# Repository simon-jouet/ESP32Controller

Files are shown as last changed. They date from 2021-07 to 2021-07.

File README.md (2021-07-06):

# ESP32Controller

ESP32Controller is an open source hardware controller for 3d printers, laser cutter/engraver and other CNC machines.

---

### Overview

There are currently 3 iterations of the board all based on either the ESP32 or ESP32-S2. The ESP32 is a dual core Xtensa LX6 with 34 GPIOs and the ESP32-S2 is a single core Xtensa LX7 with 43 GPIOs and built-in USB support.

  Board | MCU      | Drivers | Mosfets | Thermistors |  Comm. |
  ------|----------|-------- | ------- | ----------- | ------ |
  R3    | ESP32-S2 | 10      | 5       | 5           | USB
  R2    | ESP32    | 5       | 3       | 3           | USB to UART
  R1    | ESP32    | 4       | 3       | 2+2         | USB to UART

### R3 Board

This third iteration of the board moves away from the ESP32 to the ESP32-S2 to gain 9 GPIOs at the cost of having only a single core (albeit more efficient).

Using the newly available GPIOs the number of mosfets and thermistors on the board have increased to 5.

In the R2 board the I2S stream has been used to drive 5 drivers but could address more than that. In the R3 board the number of drivers increased to 10 as the cost of adding support for that many drivers is minimal and should cover most of the use cases.

This board was also designed with TMC2209 drivers in mind (although not required), by allowing UART communication for 8 of the 10 drivers through jumpers on the board and connecting the diag pins to the endstops for the first three driver slots allowing sensorless homing without external jumper wires.

  - 10 pololu stepper drivers over I2S
  - 5 mosfets
  - 5 thermistors
  - 3 endstops (connected to stepper DIAG pins for the first three drivers)
  - USB type C -- OTG port on the ESP32-S2
  - micro SD card slot
  - jumpers for UART communication to the first 8 drivers

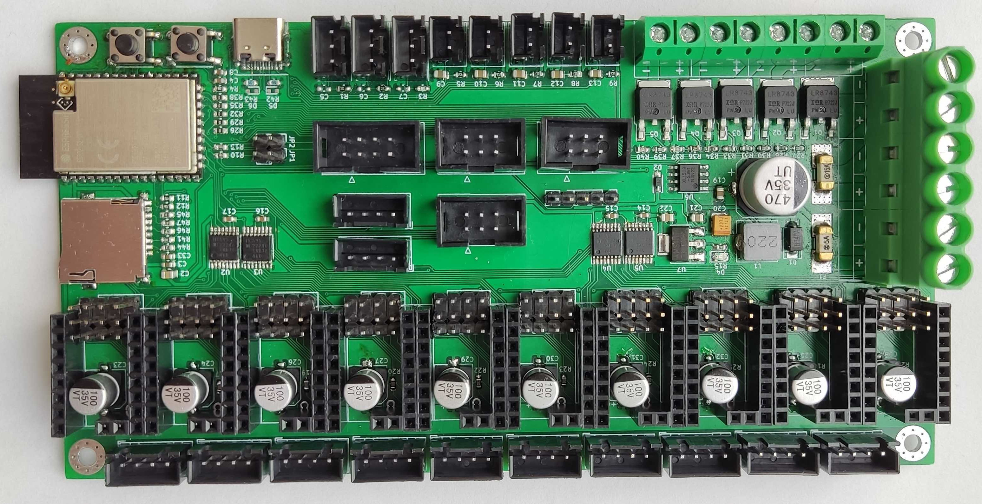
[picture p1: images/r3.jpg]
R3


### R2 Board

The primary issue with using an ESP32 as the main controller for a CNC controller is the general lack of GPIOs on the controller limiting considerably the number of drivers, thermistors and endstpos that can be controlled.

This second iteration main goal was to move away from direct GPIO control of the drivers and instead move to use the I2S stream to provide real time and highly accurate stepper pulses while only using 3 pins on the ESP32.

The redesign also removed some of the unused features of the R1 design most notably the external ADC and the GPIO expander.

  - 5 pololu stepper drivers over I2S
  - 3 mosfets
  - 3 thermistors
  - 3 endstops
  - USB type C -- CH340G USB to UART converter
  - micro SD card slot

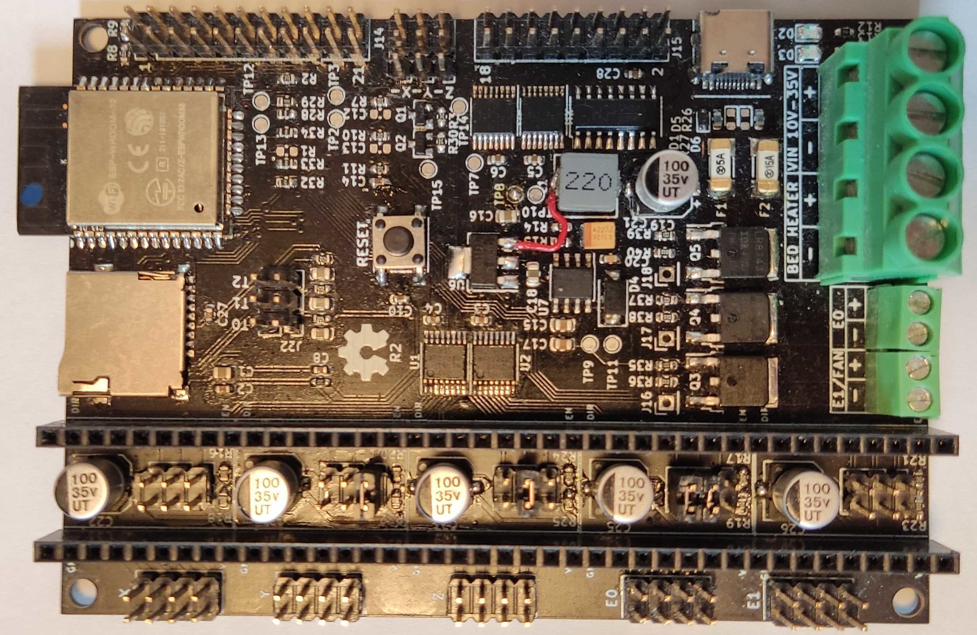
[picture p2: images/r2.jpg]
R2

### R1 Board

This is the first standalone board based on the ESP32. This board was designed as a barebone controller with the minimum required to support an i3 style printer.
 
  - 4 pololu stepper drivers (X, Y, Z, E0) with direct GPIO connection
  - 3 mosfets (Bed, Hotend, Part cooling fan)
  - ADS1015 external ADC for the thermistors (over i2c)
    - 2 thermistors to the ESP32
    - 2 thermistors to the ADS1015
  - SX1509 GPIO expander (over i2c)
    - 3 endstops direct to the the ESP32
    - 3 endstops to the GPIO expander
- USB micro b -- CH340G USB to UART converter
- micro SD card slot

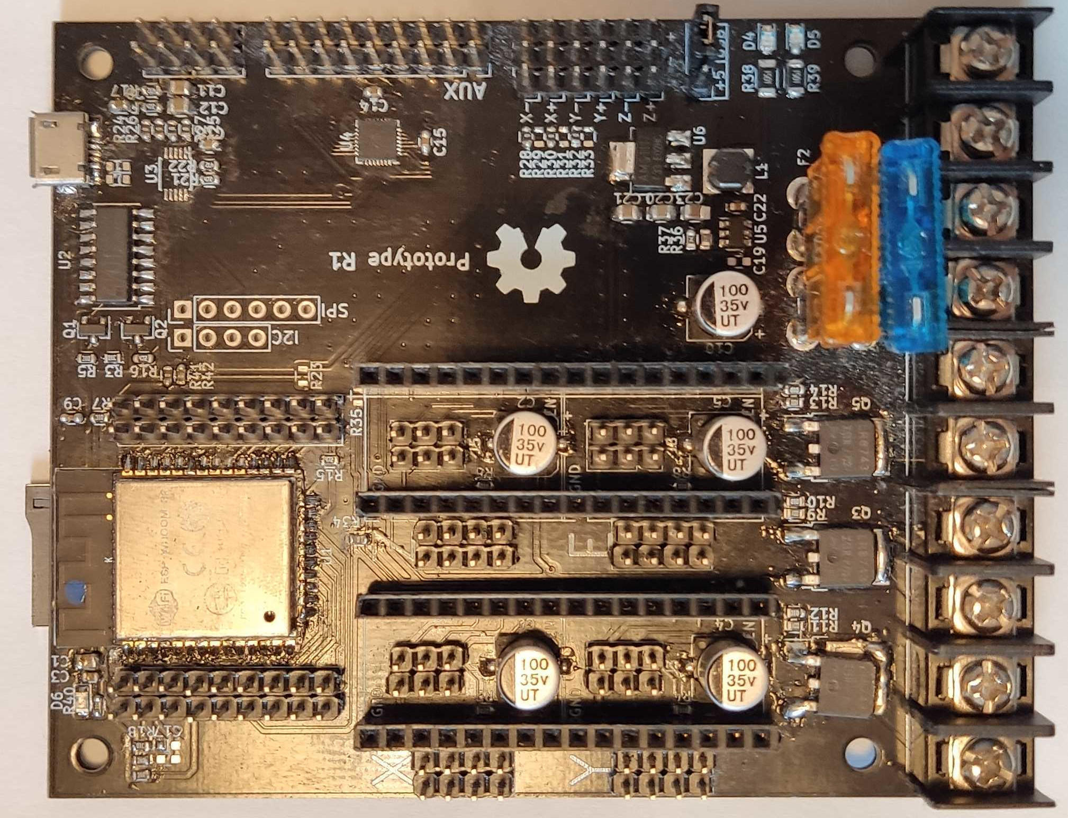
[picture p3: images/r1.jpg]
R1


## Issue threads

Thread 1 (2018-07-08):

Modifications for the R2

simon-jouet, 2018-07-08:
Somes notes for the R2 to consider

* ~~Keep the ADS1015? Either bad batch in the first run or very temperature sensitive when soldering...~~ no need for that anymore
* Add a reset button instead of relying only on DTR
* More compact PCB
* ~~Keep 24V automotive fuses? If so change the socket to something easier to solder. Maybe move to micro autotomotive fuses with sockets~~ switch to 1808 SMD fuses
* Increase the resistance of the witness LEDs as they are super bright at the moment
* Move the SD card slot to the top so the pins can be waved soldered

keyz182, 2018-07-08:
> Add a reset button instead of relying only on DTR

I'd suggest not only a reset button, but two pads or holes for a user to solder a 2 pin header to for wiring up a reset button. Reset is often used as an emergency stop, as it'll stop everything, but bring the software back up to ensure fans are kicked in where appropriate (e.g. hotend, to prevent heatcreep, and subsequent jams).

> Increase the resistance of the witness LEDs as they are super bright at the moment

Definitely! Crazy unnecessarily bright LEDs are getting out of hand :p

As the board sits currently, is it possible to pull a PWM 5v signal from somewhere (e.g. heater)? I ask because it would be interesting to use this board to run a laser cutter, which generally require a 5v PWM for intensity. For e.g. the Duet, this is done by disabling the/a heater, and using it's PWM signal.

simon-jouet, 2018-07-08:
> I'd suggest not only a reset button, but two pads or holes for a user to solder a 2 pin header to for wiring up a reset button. Reset is often used as an emergency stop, as it'll stop everything, but bring the software back up to ensure fans are kicked in where appropriate (e.g. hotend, to prevent heatcreep, and subsequent jams)

So that part is actually already the case, I broke out the pins of the ESP32 so the two top left pins in the header can already be used for that :). At the moment I reboot the board by shorthing both pins with my tweezers...

>As the board sits currently, is it possible to pull a PWM 5v signal from somewhere (e.g. heater)? I ask because it would be interesting to use this board to run a laser cutter, which generally require a 5v PWM for intensity. For e.g. the Duet, this is done by disabling the/a heater, and using it's PWM signal.

At the moment the board runs at 3.3V however there is 5V but it's not exposed (from USB or the SMPS) and regulated down to 3.3V. How much current do you need for the PWM, is it just singalling? because every output pin on the ESP32 can be PWM you can just use any of the available free pin (which isn't much) at 3.3V. You could also use the SX1509 GPIO expander that actually support PWM out - kind of depend how often you need to change the pwm frequency but that would also be at 3.3V. The SX1509 could be powered at 5V to get 5V IO but then would need level translation when talking to the ESP32. I would guess most laser that have a PWM signal input would be quite happy with 3.3V instead of 5V as most devices have high a threshold lower than that (but i'm guesssing - i have a laser module in my aliexpress cart just not ordered yet :))

keyz182, 2018-07-08:
> So that part is actually already the case, I broke out the pins of the ESP32 so the two top left pins in the header can already be used for that :). At the moment I reboot the board by shorthing both pins with my tweezers...

Awesome :)

The PWM is just signalling, so low current. Not sure what would happen at 3.3v, but yeah, it might work, would have to test. No biggie though to add an external level shifter on a separate board for that kind of thing. It's what I've just done on my Duet :)

julianobst, 2018-07-09:
According to the chapter "2.2.1.2 Positioning a ESP32 Module on a Base Board" from the [ESP32 Hardware Design Guidelines](https://www.espressif.com/sites/default/files/documentation/esp32_hardware_design_guidelines_en.pdf), it would be better for the rf performance to remove the copper under/around the antenna or better place the modules antenna outside the baseboard.

simon-jouet, 2018-07-09:
> According to the chapter "2.2.1.2 Positioning a ESP32 Module on a Base Board" from the ESP32 Hardware Design Guidelines, it would be better for the rf performance to remove the copper under/around the antenna or better place the modules antenna outside the baseboard.

Yeah you're right, the current placement is quite far from optimal. I have removed the ground plane on the top layer but not nearly enough to align with the hardware guidelines. Thanks for that I guess with the next rev the ESP is going to move to the right of the board and the antenna is probably going to stick out (which i'm not a big fan off)

julianobst, 2018-07-09:
I think a cutout under the antenna would also do the job. With a cutout you could keep the alignment of the board outline and antenna outline.

simon-jouet, 2018-07-22:
Hey guys, thinking about the R2 of the board - any suggestions on which fuses to go for? I like the automotive fuses like in the current board but they take a *LOT* of space. Did you ever had to replace a fuse - if so how often? (I never had to on my printers/boards).

I very much like https://uk.rs-online.com/web/p/fuse-blocks/7693716/ but they are not cheap. On aliexpress some 1808 SMD fuses are significantly cheaper but they are without a holder an directly soldered on the PCB.

keyz182, 2018-07-22:
They look cool, but also really fiddly to change.

The newer version of the Duet Wifi uses blade type fuses, but they're smaller than the normal automotive fuses (see the 3rd screenshot on their store - https://www.duet3d.com/DuetWifi).

simon-jouet, 2018-12-20:
I found tiny 1808 fuse holders on aliexpress for quite cheap, I ordered a bunch and should get them in January, if they are nice I might use this in the next revision of the board.

https://www.aliexpress.com/item/Hzy-Gold-foot-1808-125V-0451-SMD-Fast-blow-Fuse-0-5A-0-75A-1A-2A/32872911147.html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

simon-jouet, 2019-07-06:
closing #8

Closed 2019-07-06.

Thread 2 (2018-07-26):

[Not an issue] GRBL ported to ESP32

keyz182, 2018-07-26:
Not sure if there's a forum, or somewhere for discussion, so posting here -
https://hackaday.com/2018/07/26/grbl-ported-to-the-esp32/
Worth keeping an eye on.

simon-jouet, 2018-07-26:
hey @keyz182 thanks, yeah I saw this as well over lunch :) I posted a reply to hackaday just in case some people are interested. Regarding the forum no there is nothing for now, if people are interested I could set something up, or maybe start a thread/category on https://discuss.toms3d.org

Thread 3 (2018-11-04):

Request for BOM

vivian-ng, 2018-11-04:
Hi, do you have a BOM? I am trying to figure out what are the specifications of the inductor, mosfets, microSD card shield, diodes, transistors, etc. that you are using in your design.

simon-jouet, 2018-11-05:
Hi @vivian-ng, I've seen some of your messages, sorry for not getting back to you the last few months have been very hectic and I had very little time to dedicate to this. I don't have a proper BOM list yet but I have records of everything i've used.

- Inductor: https://uk.farnell.com/webapp/wcs/stores/servlet/ProductDisplay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
- Mosfets: https://www.aliexpress.com/item/New-IRLR8743-TO252-MOSFET/1695115706.html?spm=a2g0s.9042311.0.0.27424c4dlT22Rw
- microSD: https://www.aliexpress.com/item/10PCS-Push-Push-Type-TF-Micro-SD-Card-Socket-Adapter-Automatic-PCB-Connector-100-brand-new/32881919643.html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
- Diodes: (I think it's in the schematic? IIRC i didn't populate the TVS diodes in the dev version)
- 100uf caps https://www.aliexpress.com/item/E021-50pcs-100UF-35V-6-3mm-7-7mm-SMD-electrolytic-capacitor/32712209859.html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
- screw terminals: https://www.aliexpress.com/item/10pcs-lot-KF7-62-7-62MM-Pitch-2Pin-PCB-Screw-Terminal-Block-Connector-KF7-62-2P/32863208285.html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 (4 and 6 pins versions)
- transistor for the usb to serial https://www.aliexpress.com/item/100PCS-S9014-MMBT9014-9014-Mark-J6-SOT23-SOT-23-NPN-General-Purpose-Transistors-0-1A-50V/32854935087.html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

The rest should be just normal 805 or 603 passives so pretty much anything will do

vivian-ng, 2018-11-06:
@simon-jouet Thank you for giving the links! This will really help me in sourcing for the items.

lkvapil, 2018-11-13:
Hi,

could you share your BOM @vivian-ng ?

Thank you
Lukas

simon-jouet, 2018-11-17:
Guys if you are building one of those boards you can now ignore the ADS1015 and C16. I've figured out a way to get good temp measurements directly from the ADC on board of the ESP32 (especially if you use a revision 1).

I wanted to get rid of the ADS1015 anyway, it's not super cheap and it's a pain to solder (at least the ones I got, half of them didn't work) + we need custom support in marlin.

If you just want to get started with the ESP32 you can also ignore the GPIO expander + supporting circuitry for now. I still haven't added the support in marlin for that (but I will - this gpio expander is very nice, just a bit of a PITA to solder).

Would be great if you could get your own boards - I've been printing with mine for about 50 hours (maybe more considering the number of calibration cubes i've printed). I will try to work on marlin in the coming weeks to add support for some stuff ("eeprom", adc improvements, servo?), once the software is more mature and based on the feedbacks let's design a R2

vivian-ng, 2018-11-19:
@simon-jouet Thanks for the update! I am in the process of putting together a minimalist ESP32 board based on your design, without the GPIO expanders and such as they are not supported in Marlin. Just 4 motors, 1 hotend, 1 print fan, 1 heatbed. Have you tried @luc-github [ESP3D-adapted branch on his Marlin fork](https://github.com/luc-github/Marlin/tree/eps32_webui)? I think it is quite promising for a bare minimal ESP32, since it allows the ESP32 to be controlled via WiFi, given that it doesn't have enough pins to support an LCD controller. Of course, I am going to break out the TX/RX pins so someone with a MKS TFT can easily use it. But ESP32 running on a ESP3D-enabled Marlin firmware just sounds cool. Meanwhile, while designing the minimalist board, I am waiting for the mosfets to arrive (ordered on Aliexpress) so that I can try a jury-rigged setup.

For EEPROM support... that was one of the things that I realized too when I compiled @luc-github fork. This [article](http://tinkerman.cat/eeprom-rotation-for-esp8266-and-esp32/) has a link to an Arduino library for emulating EEPROM on ESP32.

luc-github, 2018-11-19:
I think EEPROM no need to be added there is a space on flash of 4KB for such purpose and as now ESP3D for Marlin use nvs partition instead of EEPROM partition to store settings, this space is fully free

vivian-ng, 2018-11-20:
@luc-github Yes that is basically why I pointed out that article. Arduino Core already has libraries to use ESP32's flash memory as "EEPROM" and this article has an improved version of such a library which I think can be considered for use by any who wants to add "EEPROM" support for ESP32. I was scanning through Marlin and I think the EEPROM-related code is all in one file inside the HAL subdirectory of the respective platforms.

simon-jouet, 2018-11-20:
For the screen you could use an ssd1306 oled screen I think I tried at some point and it works, I might give it another shot though.  Still it doesn't really solve the extra pins necessary if you want a rotary encoder or you might just make it with no pins to spare. My current setup is very similar to yours just a prusa i3 clone with 5steppers (2 for z in parallel) and the usual hotend, part cooling fan and heatbed with an inductive probe.Just a word of caution with your setup, it's what I did at the beginning but make sure you have a clean ground between all the components and try to plug everything (USB host + psu) on the same socket or you might have ground loops.

For the EEPROM emulation, called PersistentStore in marlin, I'm not sure yet if I want to use nvs or spliffs. The marlin api is much more similar to a file seek+write than the blob of nvs and I would rather not use too many write cycles of the flash, anyway I will have a look at that soon.

lkvapil, 2018-12-02:
Hi @simon-jouet,

are you still developing new version or it's in the states, that everything is working ?

Thank you

simon-jouet, 2018-12-02:
Hi @lkvapil,

Yeah I will probably make a second revision of the board at some point, but at the moment it does enough to port Marlin and things might change depending on what can and can't be done in software, so I'm not rushing for a new hardware revision and instead spend some time on the software (even though time has been very limited recently)

At the moment the board and Marlin works well enough to print (it's has been the fulltime board on one of my printers for about 6 months) but there are a lot of features that needs to be implemented and tested. I was hoping to have some people helping with the Marlin HAL but it seems that a lot of people have been focusing on STM32 boards instead (not too sure why, I think the ESP32 is superior in many ways although the number of IOs is a bit of an issue). Anyway, if you want to test the ESP32 for printing either get the current board and it will work or do a makeshift one like @vivian-ng and that should work too.

I'm also open to feedback on the second revision of the board (there is another issue about that). I really like the big 7.68mm connectors I used for power and mosfets because they deal with the high current without issues and you can use crimps which makes everything much nicer. Not sure everybody likes it though. I want to change the fuses to something smaller either micro automotive fuses or go for the 1208 SMD fuses (but then it's hard to swap)... One of the "main" block for a second revision right now is to get the GPIO expander to play ball with Marlin which might change some of the GPIOs allocation and therefore would need another revision of the board. I don't think it's that bad to do, just didn't really had time to work on that

vivian-ng, 2018-12-09:
@simon-jouet Just an update. I put together a Morpheus board and used that to test out the Marlin branch which @luc-github is working on. One thing I realized was the Morpheus board did not have a pull-up resistor for MOTOR_ENABLE, which caused the motors to spin when the ESP32 starts up.

Anyway, I am designing a basic ESP32 printer board (no GPIO extender, etc.) based on the Morpheus design, this ESP32Controller, and RAMPS (plus a few other 32-bit boards with schematics found online). Once the design has been confirmed to be working, I will share it on Github.

vivian-ng, 2018-12-10:
@simon-jouet @luc-github The [schematic for my ESP32-based board](https://github.com/vivian-ng/Hardware/blob/master/MRR_ESP_3DP/Schematic_MRR_ESP_3DP_v0.3.pdf) is now on Github. This is the first version which I feel comfortable with sharing, looking forward to feedback.

v0.1 was a total failure. Don't ask.
v0.2 didn't have the pull-up on MOTOR_ENABLE, and uses the 7.62mm pitch terminals given by @simon-jouet above. But I find them taking up too much space, so I went with 5.08mm pitch terminals like those found on MKS boards (which I own, and have no issues so far with the terminals) for v0.3.

v0.3:
- Basic, just ESP32 with a CH340 so that it can be accessed via USB.
- 5.08mm pitch terminals
- Pull-up on MOTOR_ENABLE
- AUX1 connector, in case anyone wants to connect to a MKS TFT, since there simply aren't enough pins for a Reprap LCD or any other type of controller using a rotary encoder.
- Design consideration is to fit this within 100mm by 100mm (currently, I am working on the PCB layout) so that people can take advantage of cheap PCB production (there is a site which offers 10 PCBs at $2 if the size is within 100mm by 100mm).
- TODO: rename all "+12V" to "VIN" and "+24V" to "VBED" which to me is largely cosmetic, but probably an important detail to real PCB designers.

Any feedback is welcome so that I can make the necessary changes before sending this for a test fabrication.

misan, 2018-12-10:
Having 24V available, why don't you use it too for powering the motor
drivers? You would get more torque at faster speeds, which is good.

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

vivian-ng, 2018-12-10:
@misan
> Having 24V available, why don't you use it too for powering the motor
drivers? You would get more torque at faster speeds, which is good.

Which is why I think a professional PCB designer will likely say my naming conventional is very poorly done. I used "+12V" and "+24V" to differentiate between two inputs, both of which can be 12V to 24V.

The way to read "+12V" is "12V to 24V".
The way to read "+24V" is also "12V to 24V", just connected to another part of the circuit.

I really need to get around to renaming it.

That said, I am also a bit uncertain about how much power the stepper drivers and motors will draw. The terminal for the heat bed is going to be passing a lot of current, and one of the reasons why I didn't connect VMOT to the "+24V" rail is because I don't want too much current through that terminal.

misan, 2018-12-10:
Consider each motor can draw around 1A.

El lun., 10 dic. 2018 9:43, vivian-ng <notifications@github.com> escribió:

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

vivian-ng, 2018-12-12:
I have changed the inputs to VIN and VBED instead of +12V and +24V, plus added a prelim PCB design. Uploaded [here](https://github.com/vivian-ng/Hardware/tree/master/MRR_ESP_3DP). All feedback welcome. Will be sending this for fabrication soon, so that I can give it a test.

Also, I created a [thread](https://github.com/vivian-ng/Hardware/issues/1) on the repo itself for further discussion on my board, so that I don't hijack this repo, which is for Simon's board.

simon-jouet, 2019-07-06:
closing this, the BOM is now in #8 and you have the thread on your repo

Closed 2019-07-06.

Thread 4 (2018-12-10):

[Not an Issue] Hint on I2S Parallel DMA and shift register stepper driving

Aggebitter, 2018-12-10:
I have thinking a lot about this I2S to a shift register. The time resolution should be good and look at this driver for RGB displays:
https://github.com/mrfaptastic/ESP32-RGB64x32MatrixPanel-I2S-DMA
https://github.com/ESP32DE/I2S_parallel_example_drive_a_64x32_display

from thread:
https://esp32.com/viewtopic.php?f=17&t=3188

simon-jouet, 2018-12-10:
Hi @Aggebitter

I've actually been wondering the same and I ordered some sn74hc595 couple of hours before you posted this :), I should get them tomorrow. Hopefully i will get some time over christmas to look into it.

I think if we want to go that way there is no need for the parallel mode of I2S, serial will be fast enough and use less IOs. From the technical reference and if i did my calculations right we should be able to achieve a bit clock of over 1MHz through I2S (40MHz word clock) for 32 outputs which should be plenty.

If we go this way there won't be a need for a GPIO expander as this will free the majority of pins on the ESP32 that we are currently using for step/dir, I just hope it won't be too much hassle getting it to work (especially because i don't have a scope handy)

simon-jouet, 2018-12-11:
@vivian-ng basically the i2s is very similar to SPI, you have some data that is sent serially (and in the case of the ESP32 can also be parallel of configurable width). So for instance you send 32bits of data 1 bit at a time or for instance 4x8 in parallel with 8 outputs. The idea (not mine) is to use the i2s bus with 595 shift registers to allow sending 32bits of data from the ESP32 to the shift registers using only the 3 i2s pins. Using this we should be able to offload the STEP/DIR/EN pins and free up many io pins on the ESP32 while still being fast enough.

So only 3 pins on the ESP32 should be needed for i2s, the data output, the bit clock and the word clock (left/right channel selection in i2s).  So the shift registers are cascaded (so it becomes equivalent to a 32 bit shift register if you use 4, QH' is chained into the next register's SER). The ESP32 i2s output becomes the first shift register SER input and the i2s bitclock and wordclock become the SRCLK and RCLK of all the registers. The output enable pin, is an input on the shift register and it's just used to enable or disable the output of the shift register, we won't need that for this so we should just tie it to ground so the output is always enabled.

Using this technique we should be able to have 32 outputs for only 3 pins used, 15 of them will be used for STEP/DIR/EN for 5 drivers (I guess adding a 5th driver make sense if we have enough outputs) and the 17 remaining can be used for other things (maybe PWM, bang bang ...) or we just populate 2 shift register as it's enough but giving additional 16 pins for ~$0.30 is probably a smarter approach

vivian-ng, 2018-12-13:
I am not very good with how Marlin works, but scanning through the files in Marlin, it seems that `stepper.cpp` under the `modules` subdirectory should be the place to implement the use of shift registers, right? To make it easily configurable, maybe a `#define` statement should be used.

For example, in `pins_ESP32.h`, something like:
```
#ifdef USE_SHIFT_REGISTER
  #define X_STEP S1
  #define X_DIR S2
  #define Y_STEP S3
  #define Y_DIR S4
...
```

Then, in `stepper.cpp`,
```
#ifdef USE_SHIFT_REGISTER
  blah blah blah code for handling movement using shift registers
...
```

 A quick search on Google shows a few Arduino libraries for shift registers. The question is how to implement them for use with stepper drivers. Is Marlin going to send out one pulse to one motor in each "cycle", or will pulses be sent in parallel to all motors being moved in each "cycle"? Meanwhile, I have zero understanding of `stepper.cpp` so I guess I will need to try and find time to understand the code if I am ever going to be able to meaningfully contribute.

misan, 2018-12-13:
My understanding is that a buffer in memory is set and I2S transfers would
be handled by a DMA channel that will be updating the serial register all
the time.

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

simon-jouet, 2018-12-13:
Yeah @misan is right this will have to be handled quite differently from the normal pins as we want to use I2s' DMA for this to be fast enough. Not too sure if we will have to update the serial continuously (which I know is how the ESP8266 examples work) or if we can actually do one-off word send. The i2s support in the ESP32 is much more mature and part of the esp-idf so I hope things are going to be a bit smoother.

Pretty sure the way to do it, is the same way as I did the GPIO expander in the old code (for the first ever board early last year). I want to keep this specific piece of code into the HAL of the ESP32 so we don't pollute Marlin's source code. The way I did it before was to use the MSB of the pin to indicate whether it is a "normal" pin or a pin on the GPIO expander. So pins lower than 128 are normal esp32 pins and pin 128 is pin 0 of the GPIO expander, pin 129 is pin 1 of the GPIO expander...

Doing it this way allows us to implement the entire logic in the HAL (https://github.com/MarlinFirmware/Marlin/blob/bugfix-2.0.x/Marlin/src/HAL/HAL_ESP32/fastio_ESP32.h) and we can abstract from Marlin the fact that these pins are not normal pins.

I received the 74HC595 yesterday, next step is going to be to solder a prototype board to try this out :)

Aggebitter, 2018-12-14:
@simon-jouet @vivian-ng
I know that I had read something about this a few years ago. Well here is those links as well
https://github.com/lhartmann/esp8266_reprap
That is based on one of the ESP8266 godfathers at
https://github.com/cnlohr/esp8266ws2812i2s

simon-jouet, 2018-12-14:
Thanks @Aggebitter I've been through this two in the last couple of days been useful to get some information but code-wise I think it will be quite different. The esp8266 example is very rough, it uses a lot of the low level registers to access the i2s peripheral. The esp-idf for the esp32 contains a proper driver so I think (hope) that the implementation will be much more straightforward and easy to follow than the esp8266 exmaples.

Regarding the board I'm just going to make a very simple board with 4 shift registers, very similar to the one in the esp8266_reprap repo. Hopefully I can get this done this weekend, designing the PCB will be very very straightforward but I want to try to engrave it using my printer so that might take a bit of time :) Once I get something running I will post it here so you can replicate it if you want (the more we are to try this the better)

For the clock of the i2s I won't go in much detail right now but the i2s peripheral works by full 32 bits word at a time even if you only use 16 bits and the maximum rate of it is (if i got it right) 160MHz / 4. So we should be able to achieve a bit clock speed of 40MHz and therefore a word clock of 40MHz/32 = 1.250MHz. What I used as a reference is a bit of a back of the envelope math, but the A4988 requires a minimum of ~4us pulse time (the TMC are faster than this but it was more to check things out). 4us is 250kHz so we've got plenty to spare even if we try to step as fast as we can. Reallistically the 74hc595 won't be able to be clocked at 40MHz but I think it should work out okay even if we go lower than that

Aggebitter, 2018-12-14:
@simon-jouet When you are ready with your prototype schematics can you post it asap ?
The shift register can't be connected in so many ways :) but what pins would you use in the ESP32 and what pins för the stepper drivers? Are we going for four 74HC595 from the start ?

I've got the time this weekend as well to build a prototype and got the tools for probing and sample the output if you run into problems.  I'm more into electromechanics than programming (just novice basic skills and knowledge in C++/C)

simon-jouet, 2018-12-16:
@Aggebitter Here is the basic schematic [i2sexpansion.pdf](https://github.com/simon-jouet/ESP32Controller/files/2683606/i2sexpansion.pdf).

I've tried to mill the PCB using my printer and it wasn't a great success (and my neighbours probably didn't like me very much) so I just it setup on breadboard for the time being. I've managed to hook up my Saleae clone logic analyzer too and it looks like it's doing the job well enough so that's a good start. (I might etch a board but my 2d printer died :D)

For the pins to use on the ESP32 I'm not sure yet and it doesn't matter too much but i'm considering using GPIO17/GPIO16 and GPIO0 so we still have all the rest available (HSPI/VSPI/I2c...)

For the 5V operation I think we might be able to get away with it without level shifting, if we want to run at 5V. We already have on the board 5V from either the USB or the buck converter than can be used to supply the shift registers and the 3.3V output of the ESP32 should be high enough for the input of the shift registers. The issue would have been if the shift registers output something to the ESP32 but that's not the case.

Now i will have to look a bit more into i2s, from the little time i spent on this yesterday it looks like the bclk and channel selection continue to run even if the transmit buffer is empty. I guess on the esp8266 example that's why they continuously send the same data, so I need to look into that either to keep queuing data, make the buffer cyclic so it resend the same data over and over again or be able to switch off the clocks when the buffer is empty.

misan, 2018-12-16:
@simon-jouet 74HC595 can work from 2 to 6V http://www.ti.com/lit/ds/symlink/sn74hc595.pdf
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
Aggebitter, 2018-12-25:
@simon-jouet  Can writing to the registers be handled by the stepper interrupt routine in Marlin ?
Why I'm asking is that with this solution the implementation to HAL should be straight forward but we do not free up cpu cycles. I'm I right ?

I was thinking complete the other way around. By giving FreeRTOS a Core0 task with decent priority just to feed the DMA ring buffer (The bigger size of buffer the lower priority). The stepper interrupt would just write to that buffer instead of pulling GPIO's. As we can toggle the stepper pins at more than 400kHz the limit is in what time resolution we would need. And the time resolution in not an issue.

As an example.  If we use a GT5 pulley with 20 tooths and 256 microsteps. The step rate will be 256 000  steps/sec and give 100mm/sec on a 200 step/rev stepper motor. If we put in the numbers that I've got (probably not maxed out yet) on the skift register that is 416 000 steps/sec and with the same hardware setup it gives us 162.5 mm/sec in movement

So what if we "miss" aka linear jitter, a step in the time domain. One micro step is 0,000390625 mm that's maximum error at all speeds for all axis! At slower rates this linear jitter will reduce more but still be there. Conclusion: We are way below the mechanical error in the stepper motor itself.

The size of the ring buffer is only a matter when the stepper movement has to interact with other interrupts as when homing and probing. But let us look at the linear jitter again. With a ring buffer at 1024 we will get a limit interrupt somewhere in the +0.4 mm range. That sounds like a bad numbers. Well that was at 162.5mm/sec probing ;-). At feed rate 60mm/min we will move 1mm/s. The ring buffer will be have a round trip of less than 0.0025 sec (ring buffer size / word clock), that is again much lower than the stepper motor error.

My thinking with the ring buffer is that we would not need any semaphores or other task write handlers for that buffer in FreeRTOS. Just do a write as it is a buffer. Add a new data flag to the function and the ring buffer could loop the same data as long as no new data has arrived. No interrupts just a loop that feeds the DMA with the same data as long as it has not change. And if
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

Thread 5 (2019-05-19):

[Question] Where to define I2S_STEPPER_STREAM and any ideas about temperature readings?

felixstorm, 2019-05-19:
Hi Simon,

thanks for your great work! I upgraded my Creality Ender 3 to use an ESP32 with TMC2208 stepper drivers connected to I2S based on your coding and on your schematic here in the r2 branch and it works like a charm - just finished my first print today!

Two questions came up that you might have an answer to:
* Where did you define `I2S_STEPPER_STREAM`? I thought it would be best suited in `pins_ESP32.h` but then it seems to be missing inside `stepper.cpp` (all moves ended up terribly slow as `STEPPER_TIMER_RATE` had been defined as if used without I2S). I ended up putting it in `platformio.ini` as a build flag, but maybe you have a better idea?
* Temperature readings vary massively. This might have to do with the ESP32s ADC - is that just the way it is or have you been able to figure out a better solution?

Thanks again for your great work and kind regards,
Felix

simon-jouet, 2019-05-20:
Hi @felixstorm,

Great to hear that you are using the HAL especially with the I2S not many people do unfortunately (although I guess when a board becomes available more people will)

> Where did you define I2S_STEPPER_STREAM? I thought it would be best suited in pins_ESP32.h but then it seems to be missing inside stepper.cpp (all moves ended up terribly slow as STEPPER_TIMER_RATE had been defined as if used without I2S). I ended up putting it in platformio.ini as a build flag, but maybe you have a better idea?

I will have to double check with my local version when I have access to it but IIRC it was defined in the HAL.h of the ESP32's hal.

>Temperature readings vary massively. This might have to do with the ESP32s ADC - is that just the way it is or have you been able to figure out a better solution?

So the ESP32 ADC is far from perfect but it should be more stable than what you describe (I also think that Marlin can be tweaked to work better especially when the ADC can be sampled quickly). The first thing to check is which version of the ESP32 you are using, the ESP R1 is much better because it contains a factory built-in calibration curve for the ADC as well the proper VREF. If you use a R0 then you can calibrate the VREF by hand (although I would just recommend switching to an R1). You can also check the voltage reference of your voltage divider make sure it's very close to 3.3V. Check that the resistors you have used have a good tolerance. And finally make sure to retune your PID.

Hope that helps, I haven't really touched this in a while, but I'm still planning to get back to it at some point :)

Simon

felixstorm, 2019-05-20:
@simon-jouet - thanks for your reply. The I2S path really seems a very clever (and cheap) way to go to get more GPOs and perfect stepper timing. I really do not know either why people do not use it more often.
For me it was quite simple: I wanted to upgrade my Ender-3 to TMC2208 and WiFi, but also wanted to keep LCD, SD card etc., so I needed the pins and so I thought to give it a try.

About `I2S_STEPPER_STREAM`: I already did some tweaks to my local copy to be able to define `I2S_STEPPER_STREAM` in `pins*.h` (where it makes sense the most IMHO since the pin numbers defined there target I2S 128+), I just need to verify that it does actually work, rebase against a current version of `bugfix-2.0.x` and then I would file a pull request to https://github.com/MarlinFirmware/Marlin.

I will post it here after I did the polishing so you can have a look and potentially object.

felixstorm, 2019-05-20:
About the temperature readings: I did do a PID retune, but I do have to check the ESP revision. It's not that the readings are off a certain amount or percentage, but they go up and down permanently between 5 and 8 °C. Do you remember if you had stable temperature readings on your printer?

felixstorm, 2019-05-20:
Ok, this would be the patch for `I2S_STEPPER_STREAM`:
```
 Marlin/src/HAL/HAL_ESP32/HAL_timers_ESP32.h | 6 ++++++
 Marlin/src/pins/pins_ESP32.h                | 2 ++
 2 files changed, 8 insertions(+)

diff --git a/Marlin/src/HAL/HAL_ESP32/HAL_timers_ESP32.h b/Marlin/src/HAL/HAL_ESP32/HAL_timers_ESP32.h
index 7fbaa5222..3d2d777de 100644
--- a/Marlin/src/HAL/HAL_ESP32/HAL_timers_ESP32.h
+++ b/Marlin/src/HAL/HAL_ESP32/HAL_timers_ESP32.h
@@ -28,6 +28,12 @@
 #include <stdint.h>
 #include "driver/timer.h"

+// need this to pull I2S_STEPPER_STREAM definition from pins_*.h based on configured board
+#include "../../inc/MarlinConfig.h"
+// need to also include pins.h explicitly here as the above statement will be ignored if HAL_timers_ESP32.h
+// is being included from inside MarlinConfig.h / HAL.h (but before pins.h)
+#include "../../pins/pins.h"
+
 // --------------------------------------------------------------------------
 // Defines
 // --------------------------------------------------------------------------
diff --git a/Marlin/src/pins/pins_ESP32.h b/Marlin/src/pins/pins_ESP32.h
index 9901dde20..dad1e0d81 100644
--- a/Marlin/src/pins/pins_ESP32.h
+++ b/Marlin/src/pins/pins_ESP32.h
@@ -40,6 +40,8 @@
 //
 // Steppers
 //
+#define I2S_STEPPER_STREAM
+
 #define X_STEP_PIN         128
 #define X_DIR_PIN          129
 #define X_ENABLE_PIN       130
```

vivian-ng, 2019-05-20:
@felixstorm One suggestion is to create a separate pins_xxxxx.h file for your current setup. This way, the pins_ESP32.h can be the standard pins file for all boards based on the ESP32 (like pins_RAMPS.h) and every adaptation of it is a separate pins file.

Also, I am curious as to how you can connect the Ender-3's LCD to this setup. I am trying to figure out how the LCD's pins work...
So far, what I can glean out for the [Creality v1.1.2 board](https://github.com/Creality3DPrinting/CR10-Melzi-1.1.2/blob/master/Circuit%20diagram/Motherboard/CR-10%20Schematic.pdf)'s LCD connector:
Pin 1: VCC 5V
Pin 2: LCD_PINS_ENABLE (connected to ATMEGA1284's SDA pin)
Pin 3: LCD_PINS_D4
Pin 4: RESET (is this the EN pin of the ESP32?)
Pin 5: BTN_ENC (connected to ATMEGA1284's SCL pin)
Pin 6: BEEPER_PIN
Pin 7: BTN_EN1
Pin 8: BTN_EN2
Pin 9: LCD_PINS_RS
Pin 10: GND
I guess for the ESP32, most of the pins to use this LCD display can be the freed-up pins (IO25, IO26, etc.) but just wondering if LCD_PINS_ENABLE must be SDA and BTN_ENC must be SCL?

felixstorm, 2019-05-20:
@vivian-ng Yes, I also did create my own board and `pins_ESP32_FS_ENDER3.h` file (https://github.com/felixstorm/Marlin/blob/Felix_Ender3_ESP32_2.0.x/Marlin/src/pins/pins_ESP32_FS_ENDER3.h), but since `pins_ESP32.h` also references stepper pins above 128 which need I2S, I thought it would be helpful to have it in `pins_ESP32.h` as well.

And for the LCD on the Ender-3 take a look at the attached PDF. This is my current setup (R160 & R161 are not populated, based on @simon-jouet's work in his r2 branch) which works nicely on my Ender-3: [201904_Esp32ReprapController.pdf](https://github.com/simon-jouet/ESP32Controller/files/3198646/201904_Esp32ReprapController.pdf)

Marlin needs a few more fixes for ESP32 to work with the current bugfix-2.0.x branch, but I will hopefully be able to file the corresponding pull requests within the next few days:
https://github.com/felixstorm/Marlin/commit/6d3199539e919592f7f4926ab2c75e227cca6d1c
https://github.com/felixstorm/Marlin/commit/01011ac973846a3e5b46db92b98409621a3e261d
https://github.com/felixstorm/Marlin/commit/6281e378af18b5389db730edb92bfff250ea2e1e
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
edsonbrusque, 2019-05-29:
Hello @felixstorm.

I'm interested about your ADC noise.

It would be useful to know if the variation is in your readings or in your actual bed temperature. Are you seeing this variation only on the display? Do you have any means to measure the actual nozzle and bed temperatures (a thermometer with a logger) or the voltage at the ADC pins (an oscilloscope)?

If the temperature variation on the LCD is very quick (like changing +/- 5% all over the place) it's probably noise on the ADC pin.

If it's a more sinusoidal variation with a more or less defined duration (like going from 195% to 205% in 10 seconds and back) it would suggest poor PID tuning.

A quick way to filter noise is using larger capacitors (C30, C31 and C32 in your schematic). 10k and 100nF (as in your schematic) give a time constant of 1 us, which is usually adequate regarding high-frequency noise.

You also can't make this time constant very large (like changing to 100 uF capacitors that will give you one entire second time constant) as the PID would probably overreact and have slow and large oscillations).

I have an Ender-3 and just learn about this ESP32Controller project. I would like to build it. Maybe it's time to order some stepper drivers... :)

felixstorm, 2019-05-30:
@edsonbrusque I still have not figured out what exactly causes the noise in the temperature readings, but due to your question I started to dig again today. Unfortunately I still do not have an answer, but I have a few findings:
* It is not due to PID tuning as there also is noise when I switch off the heater and the nozzle slowly cools down.
* Removing the step down converter and powering the ESP32 just via USB did not make a difference.
* Switching the ESP32 module to a different one that I had lying around did not make a difference.
* But: Connecting an ESP32 on a breadboard just with jumper wires on `GND`, `3V3`, `NOZZLE` and `NOZZLE_T` to my board does make temperature readings work fine. When the heater is powered, I can see nice sinusoidal variations from (probably sub-optimal) PID tuning and also when I switch off the heater there are nice decreasing readings without any errors .

Hopefully I will have some more time tomorrow and then I'll try to check wire by wire what causes the noise.

BTW: The capacitors used for the thermistors are C20 and C21 which are already 4.7 uF (and adding even larger ones did not make a difference either).

edsonbrusque, 2019-05-30:
Hello @felixstorm. It seems to me that the stepper drivers are injecting noise on your VCC (+3V3).

Is it possible to power the drivers from the +5V line?

Or can you have a separate regulator from 5V to 3V3 to power just the drivers?

The development boards don't have beefy capacitors and power regulators. I would rely on it just to power the components on the development board itself. You may even need larger capacitors (like 2 x 470uF x 16V) on the development board 3V3 just to lower the spikes caused by WiFi communication.

Maybe some bigger capacitors on the 3V3 and 5V power lines (on strategic places around the board) would help. I see that you have capacitor for the +24V line close to the drivers, but there's no capacitors for the VCC line. I would not assume that the (cheap?) stepper driver modules have adequate decoupling.

Which stepper drivers are you using?

Can you provide the board design file?

felixstorm, 2019-06-02:
It turned out for the noise on the temperature readings to be caused by the I2S lines in combination with my quick-and-dirty board layout. I had expected the whole I2S path up to the drivers to fail, but not for it to have unwanted side effects on other areas. But 2 MHz is more than I usually deal with ;-)

As I anyway had the plan to update my board layout a bit, I will do that and let post my findings up here.

@edsonbrusque I had already completely removed the stepper drivers for the tests and even the shift register ics. I also did try attaching different kinds of capacitors to the different power lines. WiFi is off currently (primarily to reduce upload and Marlin boot time). The drivers I use are FYSETC TMC2208.

Felix

felixstorm, 2019-06-08:
Finally I seem to have been successful. The third revision of my board works nicely and I do not seems to have any unusual noise in the temperature readings anymore.
Details including board layout can be found [here](https://github.com/felixstorm/Creality_Ender_3_ESP32_Board).

Thanks again for everybody's help!

Closed 2021-07-06.

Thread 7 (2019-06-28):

R2 routed?

KanyonKris, 2019-06-28:
@simon-jouet, very nice project!
The schematic looks nice. I opened the PCB layout and I see the part footprints but no traces, just the net lines. Is this correct or do I have something wrong?

simon-jouet, 2019-06-28:
Hi @KanyonKris

Thanks, I haven't routed the R2 board because I'm still tweaking it a bit, if you want to see a routed version @Ringel pushed a MR for one. I haven't tried it but if you wait a bit @Ringel should be able to tell you if it works or not.

I've done few more Tweaks to the schematic since then and will continue a bit over the weekend. I also think I've found a decent layout so the next step will be to clean that up a bit and start the routing. With the layout I've drafted for now we should have the full board in the same footprint as an arduino mega

KanyonKris, 2019-06-28:
Thanks for the reply. I'll check out Ringel's board and watch for your updates.

simon-jouet, 2019-07-06:
closing #8

Closed 2019-07-06.

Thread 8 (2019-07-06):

R2 preview and BOM

simon-jouet, 2019-07-06:
Okay so I've finished the R2 and ordered some PCBs, here is the 3d render

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

I started the BOM and my current estimated cost for the components + PCB is about ~£10 ($12.5) of course on top of that there is the assembly cost and wastage but that's very dependent on the number of boards being made (and for the time being i do it myself)

[BOM.xlsx](https://github.com/simon-jouet/ESP32Controller/files/3364564/BOM.xlsx)

While doing the BOM i've noticed I've made two mistakes in footprints for the diodes, I was hoping to get a 603 package for the diodes but that's not the case, shouldn't be too much a problem for this batch but I will have to get it fixed.

shawe, 2019-07-20:
Thanks for sharing your work.
Do you try it (or can do it) with this GRBL fork? https://github.com/bdring/Grbl_Esp32 Looks interesting have a same board that can work well with both projects.

Aggebitter, 2019-07-21:
Is there a possibility to by one assembled or un assembled from you?

Aggebitter, 2019-07-21:
@shawe The GRBL_ESP32 does not use shiftregisters for the stepper motors. But you can configure Marlin to work as an router/Mill

shawe, 2019-07-21:
Thanks for your answer @Aggebitter, then Marlin is more interesting to me at least for start. I asume that each project are more specific to each work, but don't look for if someone can do both.

I'm interested also in get one, I try a quote from jlcpcb and seems to be available 5 boards at 2$ (offer only for the first buy and also applicable for more units) but I'm not familiar to solder SMD components and also don't have the needed tools to work with that precision.

Aggebitter, 2019-07-26:
@shawe I'm running GRBL_ESP32 on my small router, even tryed to get GRBL_ESP32 interested in using shiftregisters but no response on there part.

vivian-ng, 2019-07-31:
@simon-jouet Can you share the settings you had to make in Configuration.h and pins_ESP32.h to [test out the OLED](https://github.com/MarlinFirmware/Marlin/issues/14345#issuecomment-515755280) and possibly ILI9341? I am wondering about the display/LCD option to set in Configuration.h, and the settings for SDA pin, SCL pin, I2C address for the OLED display, and the different pins for the ILI9341.

simon-jouet, 2019-07-31:
> Is there a possibility to by one assembled or un assembled from you?

For the time being I don't have enough components to assemble more than a handful of boards so probably not (I will send one to thinkyhead and probably to Luc for dev). I've ordered a few more components so i might be able to assemble a few more boards. Let's see when I get the components but I would rather not assemble too many myself as it takes a while (maybe ~2 hours per board) and sending the individual components not soldered will be a mess with the amount of SMD resistors/cap/ics. If enough people are interested we could potentially get a batch assembled in China but I'm not too sure what would be the price of that.

> @simon-jouet Can you share the settings you had to make in Configuration.h and pins_ESP32.h to test out the OLED and possibly ILI9341? I am wondering about the display/LCD option to set in Configuration.h, and the settings for SDA pin, SCL pin, I2C address for the OLED display, and the different pins for the ILI9341.

For the OLED it's relatively straightforward, just connect the screen D0 and D1 to SCL and SDA in the esp32 (pin 21, 22), connect the enable to the enable pin of the ESP32 and tie D/C to ground (https://electronics.stackexchange.com/questions/164680/ssd1306-display-spi-connection-or-i2c-according-to-resistors). Once that's connected in your configuration.h comment out `//#define U8GLIB_SSD1306` and modify your platformio.ini for the esp32 like that

```diff
 lib_deps =
+  ${common.lib_deps}
   https://github.com/me-no-dev/AsyncTCP.git
   https://github.com/me-no-dev/ESPAsyncWebServer.git
 lib_ignore  =
-  LiquidCrystal_I2C
   LiquidCrystal
-  NewliquidCrystal
-  LiquidTWI2
   TMC26XStepper
   c1921b4
-  SailfishLCD
-  SailfishRGB_LED
```

For the ILI9341 I haven't really tried yet, I had a quick look but the current code is quite specific for STM32 IIRC so there will be some dev required for that (and it's not very high in my priorities to get that working for now)

shawe, 2019-07-31:
> > If enough people are interested we could potentially get a batch assembled in China but I'm not too sure what would be the price of that.

@simon-jouet I'm asking for a quotation on PCBWay of 20 units (to get an idea), comparison price later. Maybe 20 are a lot of they at this time, I don't know, but is the most affordable option for few units.

Also, maybe there are better alternatives to make it, but this company can do it all process without wasting your time. I upload your gerber files, and your BOM list and maybe tomorrow they fill it the quotation.

Quotation at this moment:
- 2 Layers Size 102x71mm 1.6mm Product No.:W234586ASH1 [PCB Production]
  -  20 units at $37.00 - $1.85/unit
  -  5 units at $24.00 - $4.80/unit
- SMT for PCB No. W234586ASH1 [PCB Assembly ]
  -  20 units at $30.00 - $1.5/unit
  -  5 units at $30.00 - $6/unit
- Components
  - Waiting for reply of PCBWay (I edit this when receive a notification)
- Shipment
  - Unknown at this moment
- Your fees for your work

They also promoted open source: Share&Sell _This feature is for open source enthusiasts who would like to share the cool projects to others and earn commission._

Maybe this last option is more comfortable to you, and also allow us to get one fully assembled.

If anyone is interested in how this company work, I found this promoted video that is a tour on this factory https://www.youtube.com/watch?v=24ehoo6RX8w

simon-jouet, 2019-08-02:
Hi @shawe,

Thanks for looking into that, I had a brief look couple of days ago at elecrow that provides similar services but didn't go as far as asking for a quote. 20 might be reasonable, I might post on Twitter in the next few days to check who would be interested and point them to here, even if there are couple extras it's not too big a deal.

I will revise the the BOM looks like there are quite a few things that are to be fixed. But looking at the prices it seems more expensive that what I would have expected, let's see once I revised the BOM and let's see what this includes. Do you know what the total of $452 includes?

Before we go for a batch I need to slightly revise the current PCB there are two footprints that are incorrect in the current board (two diodes) and I want to add a couple of headers for the +5V and +3.3V (realised this when I tried to connect a BLTouch...)

I think the open source approach is good, it will save in admin time plus if I need to ship the board from the UK it's going to be quite expensive.

shawe, 2019-08-02:
I'm not sure with the prices, because they change it without reason and without any explanation, and not respecting what I see first day, but looking their page seems to be this:

- $37 for all PCB Production
- $410 for all PCB Assembly (this part appear first time to $30 for <5, but seems to be per unit)
- $452 for all PCB components, the double than is in your list (this part is not yet filled on the quotation, I suppose you see it on the replyed BOM)

Using this prices as reference, the board fully assembled seems to be $44.95/unit

This appears on my quotation (it's in spanish):
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

@simon-jouet if you prefer it, you can upload this files and be directly in contact with PCBWay to clarify all that you want, you only need some minuts to upload your files, and wait for the reply as I attached here.

simon-jouet, 2019-08-02:
Looks very very expensive to me, I might be missing something but here the assemble board is about 3 times the BOM which I think is a bit unreasonable. (the BOM is wrong and a bit too high but still wouldn't change much). My BOM is ~£10 ($12) including the PCB with components that have been shipped individually from China. Here the cost components is higher while they weren't shipped, and the BOM price doesn't include the PCB. Finally we probably need to add shipping + import duties on top of that.

The prices in my BOM are in GBP (£) and they use ($) so their is some difference from that, but even with that there is quite a big difference.

I might check with Elecrow to see how much that would be and I might ask around to see if people have some info about this and if anyone has some experience with that please let me know :)

shawe, 2019-08-02:
I think the same, it's a big difference, maybe they are using another components in comparison with your list. Maybe later I can check component to component to found the problem comparing both BOM list.

The good part, is that they include part numbers, and can be checked or change it to some specific parts, reducing this difference but require an additional check that maybe is also need with Elecrow.

shawe, 2019-08-02:
I use the BOM replied by PCBWay, and fill it with Mouser and Digikey prices (always per unit, I know is the most expensive way) and probably I do a mistake some parts. Also there are some parts that I don't know how to found it.

Anyway, the final price is a little less than buying all individually, but of course not at same price than buying at the next level for quantity and also DIY.

[W234586ASH1-20sets-BOM 2019-8-1.xlsx](https://github.com/simon-jouet/ESP32Controller/files/3462677/W234586ASH1-20sets-BOM.2019-8-1.xlsx)

The PCB Assembly on Elecrow must be very similar, because they also have an online estimate quotation, and the price is calculated based on unique parts, holes, SMT pads, ... I don't fill this form on PCBWay, I only attach the BOM that is incomplete to a quotation and wait for a more realistic quotation.

If I'm not wrong, this form is not well completed on the other site, because I get the same start price with Elecrow. It's filled like in this image:

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

shawe, 2019-08-16:
Sorry for saying this again, but people from PCBWay are asking me again if the BOM list was reviewed with things they attached on file to be able to finish the quotation.

Closed 2021-07-06.

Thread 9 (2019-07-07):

Malyan, and monoprice have been paying attentoin and made a control board using the ESP32 SoC

Sniffle, 2019-07-07:
This is the control board in use on the Monoprice MP10 and MP10 Mini, which is rebranded from Malyan with part numbers MA10 and MA10 mini.

https://imgur.com/a/0MB0AIy

If the imgur album link fails, I will make the images public and link to them directly.

The SoC in use seems to be the ESP8266EX, which has a touch display attached to its back, a daughter board for USB and SDCard.  A 16pin ribbon cable runs to the heater and stepper board.  power is input from the power supply to the stepper control board and send along the 16 pin cable to the ESP32 main control.

That's as far as ive had a chance to dig into this.

If this piques your curiosity I'd be happy to put time towards helping get this done.  If there is any information, pictures, diagnostics, etc.  Id be happy to help.

display and ESP control board - https://www.monoprice.com/product?p_id=39107
Stepper heater board - https://www.monoprice.com/product?p_id=39106

simon-jouet, 2019-07-10:
Thanks @Sniffle for the info, it would be good to have a better look at it.

My first impression is that the esp32 is not used for printing but is used a the "screen" for the printer. My guess is that the ESP32 drives the screen and provides a webUI but the printing is done by another microcontroller (likely an atmega) and the ESP32's serial is connected to the Atmega's serial.

I might be totally wrong and would be nice to see a manufacturer using the ESP32 directly. But if you look at https://images.monoprice.com/productlargeimages/391062.jpg you can see below the capacitor a QFP package with what looks like 64 pins.

Ringel, 2019-07-10:
Its a ESP8266 - not a ESP32!
Yes looks like it drives the display ... maybe via the 2 8bit shiftregisters 74HC164 and the XPT2046 Touchcontroller

Something like https://github.com/luc-github/ESP3D might be running on it.

Sniffle, 2019-07-10:
I'll get some better pics of the driver board.

My initial though was also that it was display driving an atmega but I couldnt find the chip initially.  I'll take better pics and see what pops out

Closed 2021-07-06.

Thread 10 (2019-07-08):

I2S motor and FET issues

vivian-ng, 2019-07-08:
As @simon-jouet mentioned in [PR#6](https://github.com/simon-jouet/ESP32Controller/pull/6) about starting a new issue to discuss the I2S-related motor and FET issues, I have taken the liberty to open the issue.

I am also experiencing issues with the I2S stream for motors, similar to what @Ringel mentioned. Sometimes, after the motors have stopped, it will start to drift on its own (I see this on my X axis, which uses the pins 128, 129, and 130). I also had an experience where partway through a print, the X gantry just drifted toward X_MIN, and kept crashing into the endstop until I had to turn off the printer. It seemed random because I did the same print again and the print completed.

As for driving of FETs, I am able to drive my E0 MOSFET using pin 140, but I am not able to control my fan MOSFET using pin 141. I will check to see if using a pin from 144 and higher will give more consistent results.

I have horrible temperature reading fluctations of plus minus 5 degs, which could be due to noise from the I2S lines as mentioned by @felixstorm before. Will try to reroute the lines and add a ground plane below the I2S lines to see if it helps. Meanwhile, I had to set TEMP_HYSTERESIS as 10 to allow for printing to commence. Definitely not ideal, haha.

I haven't had any luck with trying to drive the LCD controllers via I2S, but will try to use the pins 144 and above to see if it works. If my understanding of what @simon-jouet is saying, the lower pins (128 to 143) should be used for the motors, while the higher pins (144 to 159) can be used for MOSFETs and LCD. Will give that a try.

simon-jouet, 2019-07-08:
> I am also experiencing issues with the I2S stream for motors, similar to what @Ringel mentioned. Sometimes, after the motors have stopped, it will start to drift on its own (I see this on my X axis, which uses the pins 128, 129, and 130). I also had an experience where partway through a print, the X gantry just drifted toward X_MIN, and kept crashing into the endstop until I had to turn off the printer. It seemed random because I did the same print again and the print completed.

Do you see it for the other steppers too are just X ? Because all the steppers are part of the same stream so I would assume that if it's something to do with I2S then all steppers would be jittering not just the X axis.

I have seen something similar to this in my first ESP32 prototype (without I2s) where the noise was triggering the stepper drivers when it shouldn't. If you have an oscilloscope put a probe on the step pin of the X driver to start with and check if you just get a peek or not. Then you can put a probe on SDI/WCLK/BCLK to see if you also see some noise.

> but I am not able to control my fan MOSFET using pin 141.

IIIRC the fan in Marlin is a PWM output so it won't work over I2S as is. Considering the FAN speed is part of the planner block it might be possible to simulate a PWM signal using the I2S stream but that's not implemented yet.

> I have horrible temperature reading fluctations of plus minus 5 degs, which could be due to noise from the I2S lines as mentioned by @felixstorm before. Will try to reroute the lines and add a ground plane below the I2S lines to see if it helps. Meanwhile, I had to set TEMP_HYSTERESIS as 10 to allow for printing to commence. Definitely not ideal, haha.

This points to roughly the same thing as the first point with the stepper moving just because of the noise. I will see how it looks with my new board hopefully the noise isn't too bad. What you can try in the short term is to reduce the noise of your board. If you have some aluminium or copper tape you can add some on top of the traces and create a grounds plane without have to reroute everything. Won't be pretty but at least you might be able to debug what's wrong.

> I haven't had any luck with trying to drive the LCD controllers via I2S, but will try to use the pins 144 and above to see if it works. If my understanding of what @simon-jouet is saying, the lower pins (128 to 143) should be used for the motors, while the higher pins (144 to 159) can be used for MOSFETs and LCD. Will give that a try.

This can be configured but that's about it yes. In the current configuration the lower 16bits are buffered in the I2S DMA stream and are perfect for time critical operation (with a bit of latency), all the operations in this stream are scheduled every time the DMA buffers finishes a block. The higher 16bits are a constant I2S channel value which is read from an I2S register so this will change as soon as the value is written. However, the constant channel is not very accurate timing wise because it will happen at the next word transmission of the I2S depending on when the register was written too, so if you write too fast some data might never have been sent.

Ringel, 2019-07-08:
The Motor drift was on all 3 Axis in my Delta configuration after a Z-move - looks like the last move was somehow sticky. I checked this with a scope on BCLK and SDI - there was a pulse every 32ms - and even after motor disable timeout the enable was still there for 4 BCLK's with a pulse within.

And i still have sometimes strange null output after 4ms - considering 250khz BCLK rate there might be something wrong every 1k/4k samples?!?

Noise might be an issue with my current design - we should consider some serial termination resistors to improve signal integrity. But Noise shouldn't be that regular - the error condition stays forever with constant frequency.

Temperatures are quite stable (using 22uf caps instead of 10us) - but having 26°C when breaking the wire won't trigger an exception. Maybe some voltage divider might give some more headroom for low temps.

BTW - got the FETs for heating up at I2S Output >16 .... but still having problems with the fan. Maybe because the HAL tells Marlin that there are no PWM Outputs above 34

vivian-ng, 2019-07-08:
For PWM implementation on I2S, will this library be good reference?
[CryptoIO](https://github.com/Crypter/CryptoIO)
In its `analogwrite()` and `run()` methods.
Basically, the `run()` method seems to be the one that decides the 1 and 0 values for each bit in the register. For an analog output bit, every 256 cycles, it is set to 1 for the number of cycles equal to its "PWM" value.

As for temperature readings, I will try out with a 22uF capacitor to see whether I get more stable readings.

Regarding noise affecting the stepper motors, I didn't really notice on Y and Z axis, but Z is on a lead screw so any small stray steps may be too small to notice, which Y is a bed and the stray steps may not create enough torque in the first place. Will try to hunt down some copper tape...

simon-jouet, 2019-07-08:
> The Motor drift was on all 3 Axis in my Delta configuration after a Z-move - looks like the last move was somehow sticky. I checked this with a scope on BCLK and SDI - there was a pulse every 32ms - and even after motor disable timeout the enable was still there for 4 BCLK's with a pulse within.

I've got a faint memory of a potential issue when the I2S data stream was set high for the last word of the buffer (because then there was no buffer afterwards to set it low). Might be something like that, might be  a bit hard to replicate.

Every 32ms would map to that, each buffer is 4k in size and therefore contains 1k samples. At 250khz the 32ms would be the 8 buffers in the dma repeating again and again when there are no movements. I will have a better idea when I get my board (and if i can replicate it)

> BTW - got the FETs for heating up at I2S Output >16 .... but still having problems with the fan. Maybe because the HAL tells Marlin that there are no PWM Outputs above 34

Marlin expects hardware PWM, and doing PWM over I2S would effectively be software.

> For PWM implementation on I2S, will this library be good reference?

Potentially, although coding the PWM over I2S is fairly straightforward just needs some time. If you want a very basic PWM over i2s you just need to set x out of 256 bit high when scheduling the stepper steps. x in that case will be the duty cycle.

Ringel, 2019-07-08:
The drift issue should be fixed if the DMA buffer is filled completely like https://github.com/Ringel/Marlin/commit/9a50f1ffbc83878bbb247522eb7a4da8db8b1b05
Wasn't able to reproduce the drift with this patch.

@simon-jouet do you still have the 16Bit DMA/16Bit Register configuration? Only found a 16Bit-Only in esp32-i2s and the 32Bit DMA in  esp32-i2s-dma

felixstorm, 2019-07-09:
@vivian-ng I personally use I2S pins for fans, but only for the controller and the hotend fans, so no PWM here. But when browsing the code to find out how these fans work, I did stumble across the define `FAN_SOFT_PWM`. And from a quick look at the code this should probably do exactly what you are looking for also for the part cooling fan and I do not see any reason why it should not work on the ESP32...

@Ringel Thanks for your fix. I will try it out when I do my next prints - unfortunately I do not have much spare time at the moment.

simon-jouet, 2019-07-09:
> The drift issue should be fixed if the DMA buffer is filled completely like Ringel/Marlin@9a50f1f
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
felixstorm, 2019-07-13:
Please don't get me wrong - I'm not for a fork either. It was just meant as a last resort for some time until the Marlin maintainers e.g. have released 2.0 and have a bit more time again.

luc-github, 2019-07-13:
@Idorobots, sorry I did not react when you pushed your PR as I am not watching Marlin git, I was overflowded with Marlin notifications and I unsuscribed a while ago, and still unwatch, I just react when my name is mentionned ^_^.
@simon-jouet Yes my FR was an open discussion - but I think it useless to start anything if it is a no go, so I asked first.

@felixstorm, yes it is not my plan neither to maintain a long term Marlin's fork, I just did it to have full tested solution before proposing a PR to Marlin. I rebase on demand without issue until then.

About @thinkyhead, I think he is busy and does not need a new reminder because @vivian-ng already did it and he is definitly aware of ESP3D since @Grownseed PR as I was mentionned on it and answered, and he recently watched a youtube video about it and commented it. 😸. But you can do some lobbying  I am ok. ^_^

That said Sorry @simon-jouet to hack your thread with such unrelated issue - but I happy to learn  steppers are better with i2s

felixstorm, 2019-07-14:
@simon-jouet An almost 12 hour PETG print (that had a large layer shift on a previous attempt a week or two ago) finished nicely and without any problems on my ESP32 Ender-3 this morning (with I2S fix https://github.com/Ringel/Marlin/commit/9a50f1ffbc83878bbb247522eb7a4da8db8b1b05 and with your new temperature code). Some stringing, but that's definitely neither Marlin's nor the ESP32's fault :wink:.

@luc-github I would just go ahead and file some small separate PRs - starting with the ones entirely inside the ESP32 HAL, e.g. one replacing EEPROM SPIFFS with NVS, another one with your synchronous WebServer implementation (as an alternative using `#ifdef`s) and then wait for them to be merged. If that's done, then file the last one offering a general method for HAL-specific g-code (maybe similar to the way `HAL_INIT` [used to work](https://github.com/thinkyhead/Marlin/blob/064177154ce7912293efa67c7e0dfcaa4a7301ec/Marlin/src/Marlin.cpp#L828) before it had been made mandatory) and containing your ESP3D specific g-codes again inside ESP32 HAL.
And if there should be no reaction, then I'd be happy to comment and agree on the pull requests and maybe @simon-jouet, @Idorobots and some others could do the same.

I'll be off for vacation more or less today for almost 3 weeks, but I'll try to monitor the discussion on my mobile if I have a chance (just copy me on any new issues or PRs). And looking forward
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

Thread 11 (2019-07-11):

PoC Octoprint compatibility

simon-jouet, 2019-07-11:
(That's Marlin related but there are more people here than on my dead Marlin branch :))

Just spent some time tonight to write the minimum required to have octoprint upload and print compatibility. Slic3r-PE looks to be quite happy with it and I can see the file being uploaded properly and the M23/M24 queued properly to start printing. That's really just a proof of concept, just wrote the software with my ESP32 board not connected to any printer.

I will clean that up and probably test it more later, just wanted to post it here if anybody is interested.

Note: If you try, a big limitation right now is that you need to specify a filename in Slic3r that follows the 8.3 format (for instance test.gco) otherwise it will fail.

```diff
diff --git a/Marlin/src/HAL/HAL_ESP32/web.cpp b/Marlin/src/HAL/HAL_ESP32/web.cpp
index b2bb03d71..a3c1cadc2 100644
--- a/Marlin/src/HAL/HAL_ESP32/web.cpp
+++ b/Marlin/src/HAL/HAL_ESP32/web.cpp
@@ -26,6 +26,7 @@

 #if ENABLED(WEBSUPPORT)

+#include "../../sd/cardreader.h" // O_* conflict with posix in idf
 #include <SPIFFS.h>
 #include "wifi.h"

@@ -35,7 +36,55 @@ void onNotFound(AsyncWebServerRequest *request){
   request->send(404);
 }

+void onUpload(AsyncWebServerRequest *request, String filename, size_t index, uint8_t *data, size_t len, bool final) {
+  if (index == 0) {
+    // TODO need to deal with 8.3 filename
+    card.openFile(&filename[0u], false);
+  }
+
+  // Write the chunk
+  card.write(data, len);
+
+  // On the final chunk
+  if (final) {
+    card.closefile();
+
+    // If requested to print, enqueue the file
+    if (request->hasParam("print", true)) {
+      AsyncWebParameter* p = request->getParam("print", true);
+
+      if (p->value().compareTo("true") == 0) {
+        card.openAndPrintFile(&filename[0u]);
+      }
+    }
+
+    // TODO send the response, not required for Slic3r
+}
+
 void web_init() {
+  server.on("/api/version", HTTP_GET, [](AsyncWebServerRequest *request) {
+    request->send(200, "application/json", "{\"api\": \"0.1\", \"server\": \"1.3.10\"}");
+  });
+
+  server.on("/api/files/local", HTTP_POST, [](AsyncWebServerRequest *request) {
+    request->send(200);
+  }, onUpload);
+
   server.addHandler(&events);       // attach AsyncEventSource
   server.serveStatic("/", SPIFFS, "/www").setDefaultFile("index.html");
   server.onNotFound(onNotFound);

```

simon-jouet, 2021-07-06:
closing this, I'm rewriting the web server to use esp-idf httpd instead of AsyncWebServer, the perf should be significantly better

Closed 2021-07-06.

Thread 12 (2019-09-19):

Brownout reset problem.

reddomon, 2019-09-19:
Hi, i am experiencing brownout reset issues. I double check power module, use 10A 5V and even splitted esp32 from 5v and powered 5A 3V but nothing changes. When homing, randomly brownout reset occurs but when printing begins prints perfectly and no brownout reset. PS I added directly a 100uf cap on esp32 module power pins.

vivian-ng, 2019-09-19:
@reddomon Are you sure it is brownout reset? Maybe connect the board to a computer, and see what the serial output is.

I had random resets when homing before, turned out it was noise from the endstops that triggered the EN pin. Added a capacitor between the EN pin and GND and it helped to get rid of the resets.

reddomon, 2019-09-19:
Thanks for your reply. Yeap I am pretty  sure. Serial output says it is brownout reset. I will give a try with your suggestion. But if it was noise, why serial output says brownout reset.?  :(

reddomon, 2019-09-26:
I tried many things but did not solve my problem. added a cap between EN and GND pin that @vivian-ng suggested bu it did not work.added 100uf ceramic cap didint work, 100nf didbnot work, seperate 3.3 v powersupply did not work, seperate 5v powersupply did not work. I even soldered directly to esp32 module 100uf and 100nf caps bu it did not work either. I lost my mind.

Aggebitter, 2019-10-05:
@reddomon BOR in my experience happens often when WiFi gets enabled (300-400mA current peak).

If you can connect an Oscilloscope at the 3.3V rail. check the voltage when homing.
Is there any drop in voltage on the 3.3V rail ?
Is there a drop in voltage when end stops are activated ?

A fast Multimeter might catch a voltage drop as well but often the voltage drop is very short.

An other issue is the internal reference voltage on some rev of ESP32.
You can test (not attached to any GPIOS) if it's an chip issue by connecting the 3.3V to a external power supply that can deliver more than 1A. Run a common WiFi sketch. If it doesn't work you might have a "bad" ESP, I had some of those. The issue is that the internal reference voltage trigger is at 1.1V +-10% below that BOR is tripped. But I'm sure that this part is not tested at factory. I always use a electrolytic cap at the 3.3 rail as an extra current buffer. but on the "bad" ones I still get BOR some times

reddomon, 2019-10-05:
@Aggebitter Hi. Wifi is not enabled and i tried 3.3v 5A Meanwell powersupply, but did not work. When i examine with oscilloscope doesnt catch any negative spike. Tried diffrent brand esp32. I will test again for 3.3v voltage drop. I think I have a clone card,because doesnt have any namings on it.
P.S. Sometimes 3 or 4 times BOR occurs repeatedly.

vivian-ng, 2019-10-20:
@reddomon Are you able to connect to the ESP32 via serial terminal to see what are the error messages that are thrown when brownout occurs? If there is something like a stack trace that is thrown, it would help if you can get the stack trace decoded so that we can see where the error actually occurred.

For my case, I had
```
Guru Meditation Error: Core  1 panic'ed (Coprocessor exception)
Core 1 register dump:
PC      : 0x400f418e  PS      : 0x00060931  A0      : 0x800f2abd  A1      : 0x3ffbe620
A2      : 0x00000000  A3      : 0x00000001  A4      : 0x3f000000  A5      : 0x00000000
A6      : 0x637f0000  A7      : 0xcc800000  A8      : 0x800f4188  A9      : 0x3ffc3080
A10     : 0x00000000  A11     : 0x3ffb0060  A12     : 0x40083907  A13     : 0x3ffbe7c0
A14     : 0x02ffffff  A15     : 0x00000000  SAR     : 0x00000020  EXCCAUSE: 0x00000004
EXCVADDR: 0x00000000  LBEG    : 0x40002390  LEND    : 0x4000239f  LCOUNT  : 0x00000000
Core 1 was running in ISR context:
EPC1    : 0x400f418e  EPC2    : 0x00000000  EPC3    : 0x00000000  EPC4    : 0x40082a51

Backtrace: 0x400f418e:0x3ffbe620 0x400f2aba:0x3ffbe700 0x400f15a6:0x3ffbe720 0x400f1613:0x3ffbe740 0x400f509f:0x3ffbe760 0x400f50bf:0x3ffbe780 0x40080fa5:0x3ffbe7a0 0x40081859:0x3ffbe7c0 0x40083904:0x3ffb1d80 0x4008362b:0x3ffb1da0 0x4008132f:0x3ffb1dc0 0x400ee6f3:0x3ffb1de0 0x400ee9a0:0x3ffb1e00 0x400e1343:0x3ffb1e30 0x400f2bae:0x3ffb1e50 0x400f1e77:0x3ffb1e70 0x400f1f3a:0x3ffb1ed0 0x400e3295:0x3ffb1f00 0x400e4b0b:0x3ffb1f30 0x400e52ad:0x3ffb1f50 0x400e695c:0x3ffb1f70 0x400e15c5:0x3ffb1f90 0x40107529:0x3ffb1fb0 0x400884a5:0x3ffb1fd0
```
And it seems to suggest an error occurred in
```
Stepper::endstop_triggered(AxisEnum) at Marlin/src/module/stepper.cpp line 2228
```

You can decode the stack trace using this [tool](https://github.com/me-no-dev/EspExceptionDecoder).

I suspect the issue is with how I2S handles `count_position` because this only seems to occur when using I2S on a coreXY setup. But we will probably need someone like @simon-jouet to advise since I am not very sure how the I2S implementation works with the ISR.

reddomon, 2019-10-20:
I will try rightaway and add results

vivian-ng, 2019-10-21:
@reddomon While you are testing, can you also try out this [possible solution](https://github.com/luc-github/Marlin/issues/1#issuecomment-544181235)?

Basically, it seems that there is an issue with using float calculation in the `endstop_triggered` function. When I used `/ 2` instead of `0.5f *`, it seems to solve the reset issue with coreXY. Just need someone else to confirm.

reddomon, 2019-10-21:
Hi @vivian-ng I tried divide 2 instead of 0.5f is working like a charm. 250+ homing cycles tried and no more brownout reset or any other reset issues. Thank you for your effort. Se you an another problem  :). By the way I am working on an nextion display controller for marlin 2+.

misan, 2019-10-21:
A double would do just fine too.
http://fightpc.blogspot.com/2018/04/moving-code-from-esp8266-to-esp32.html

reddomon, 2019-10-21:
You said that Fpu is not permitted on ISR, but double is performed by software so it is permitted. Thank you for your contribution @misan .

misan, 2019-10-21:
@reddomon What I understood is that FPU registers are not saved during the ISR, so using the FPU is not allowed there. Both integers, longs, and doubles seem to work ok as they do not use the FPU. The integer solution is the fastest, but I mentioned this as in some other cases floating-point might be needed and using doubles may enable that (though it is slower).

vivian-ng, 2019-10-21:
My bad, I forgot to add the link to why float cannot be used in interrupts.

[Crash in timer interupt when data type "float" is used](https://esp32.com/viewtopic.php?t=1292)

This is actually a known issue for a while, but the Marlin firmware never really had ESP32 support until sometime last year, and I don't think many of us were playing around with coreXY+ESP32 and so this problem was not discovered for a while.

Hopefully, someone can make the necessary changes and push a PR back to MarlinFirmware. Maybe encapsulate the changes inside #ifdef ESP32 statements so that it does not affect other platforms. I would do it if I could, but unfortunately, my fork of Marlin is based on luc's and we are still [pending decision on how his fork can be merged back to Marlin](https://github.com/MarlinFirmware/Marlin/issues/14390).

Closed 2019-10-21.

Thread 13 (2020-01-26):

ESP32 wifi mode problem

reddomon, 2020-01-26:
Hi. When I compile if wifi is enabled, ESP32 is resetting. Try different libraries and different code stack nothing solved the problem. I am sending M20 via serial. Then M23 some.gcode and after sending M24 start gcode command an unknown reset occurs. Reset reason was Heap Corruption.

reddomon, 2020-01-26:
Here is the decoded stack trace:

PC: 0x40084aa4: heap_caps_malloc at /home/runner/work/esp32-arduino-lib-builder/esp32-arduino-lib-builder/esp-idf/components/heap/heap_caps.c line 93
EXCVADDR: 0xa5a5a5c1

Decoding stack results
0x40084aa4: heap_caps_malloc at /home/runner/work/esp32-arduino-lib-builder/esp32-arduino-lib-builder/esp-idf/components/heap/heap_caps.c line 93
0x40084b31: heap_caps_malloc_default at /home/runner/work/esp32-arduino-lib-builder/esp32-arduino-lib-builder/esp-idf/components/heap/heap_caps.c line 140
0x40084ff5: _malloc_r at /home/runner/work/esp32-arduino-lib-builder/esp32-arduino-lib-builder/esp-idf/components/newlib/syscalls.c line 37
0x401526ff: operator new(unsigned int) at /builds/idf/crosstool-NG/.build/src/gcc-5.2.0/libstdc++-v3/libsupc++/new_op.cc line 50
0x400e16a1: AsyncWebSocket::makeBuffer(unsigned char*, unsigned int) at .piolibdeps\esp32\ESP Async WebServer\src\AsyncWebSocket.cpp line 1207
0x400e1e40: AsyncWebSocket::textAll(char const*, unsigned int) at .piolibdeps\esp32\ESP Async WebServer\src\AsyncWebSocket.cpp line 960
0x400e1e55: AsyncWebSocket::textAll(unsigned char*, unsigned int) at .piolibdeps\esp32\ESP Async WebServer\src\AsyncWebSocket.cpp line 1096
0x400d260b: WebSocketSerial::write(unsigned char) at Marlin\src\HAL\HAL_ESP32\WebSocketSerial.cpp line 134
0x400d350f: serialprintPGM(char const*) at Marlin\src\core\serial.cpp line 37
0x400d5976: GcodeSuite::host_keepalive() at Marlin\src\gcode\gcode.cpp line 883
0x400d323e: idle() at Marlin\src\Marlin.cpp line 671
0x400dad84: Planner::synchronize() at Marlin\src\module\planner.cpp line 1541
0x400d66d1: GcodeSuite::G4() at Marlin\src\gcode\motion\G4.cpp line 36
0x400d529b: GcodeSuite::process_parsed_command(bool) at Marlin\src\gcode\gcode.cpp line 208
0x400d5901: GcodeSuite::process_next_command() at Marlin\src\gcode\gcode.cpp line 826
0x400d6ef0: GCodeQueue::advance() at Marlin\src\gcode\queue.cpp line 885
0x400d329d: loop() at Marlin\src\Marlin.cpp line 1173
0x400e9f69: loopTask(void*) at C:\users\red\.platformio\packages\framework-arduinoespressif32\cores\esp32\main.cpp line 19
0x40088c65: vPortTaskWrapper at /home/runner/work/esp32-arduino-lib-builder/esp32-arduino-lib-builder/esp-idf/components/freertos/port.c line 143

reddomon, 2020-01-26:
Solved disabling websocket extension. Web server works as expected, async web file upload works as expected but couldn't find the reason behind the reset issue.

vivian-ng, 2020-01-27:
@reddomon Just to get some details so that others can provide better responses.

What version of Marlin are you using? 2.0.x or bugfix-2.0.x? If possible, which commit (or around what date of the commit)? Marlin bugfix-2.0.x is under active development, so it helps to test with latest commit of bugfix-2.0.x to see if the problem still exists.

reddomon, 2020-02-23:
Sorry about the delay. I am using Marlin bugfix-2.0.x branch updated recently.

Closed 2020-04-25.

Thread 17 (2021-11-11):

Generic I2S questions

petervanderwalt, 2021-11-11:
Hi!. I am experimenting with TMC5161 drivers, on a breadboard setup running an ESP32 with the I2S expanders.

I have just about everything else working, i can control dumb drivers just fine, but I don't seem to be getting the CS pin to switch for spi transactions to the TMCs.

Verified with a scope, activity on SCK and MOSI, but CS just stays high. Do you know if its possible to use on of the I2S expansion pins as a CS pin for the Trinamics (no spare GPIOs on the ESP32, and I know Esp32_Grbl can use the I2S pins as CS pins for TMC and

M122 reports ALL HIGH so I know its a comms issue, and not seeing CS go low at the start of the transaction makes me suspicious of whether I can use I2S CS pins in Marlin?

Also, can I run more than 32 bits? For example, can I run 6* 595s for 48 extra Outputs? (step/dir/enable/cs for drivers; fets for heaters, laser, fans, rgb leds; rc-servo/bltouch, etc)

Can one run Servo's off the I2S?

simon-jouet, 2021-11-11:
Hi @petervanderwalt

> Do you know if its possible to use on of the I2S expansion pins as a CS pin for the Trinamics (no spare GPIOs on the ESP32, and I know Esp32_Grbl can use the I2S pins as CS pins for TMC and
> M122 reports ALL HIGH so I know its a comms issue, and not seeing CS go low at the start of the transaction makes me suspicious of whether I can use I2S CS pins in Marlin?

So I've personally just used GPIO's on the ESP32 for CS as timing wise use the GPIO expander can be finicky but there is no real reason why it wouldn't work (except timing). If the line stays high then there might be something else going on. Did you configure Marlin properly to have the first 16 bits as the stepper stream and the other 16 bits as the "pins"? If you have the default configuration IIRC all 32bits will be the steppers stream which won't allow you to use them as GPIOs.

If you are still in the experimentation process you could try with an ESP32-S2, I've got a version of Marlin for it too (not pushed yet) and it gives access to quite a few more GPIOs which is nice.

> Also, can I run more than 32 bits? For example, can I run 6* 595s for 48 extra Outputs? (step/dir/enable/cs for drivers; fets for heaters, laser, fans, rgb leds; rc-servo/bltouch, etc)

Out of the box no, but making the I2S code work over 64 bits instead of 32 should be fairly straightforward.

> Can one run Servo's off the I2S?

Kind off but I wouldn't recommend it. You would need to have a PWM software implementation for the I2S stream, it would be fairly straightforward to code but it would also use CPU cycles. For some things that are timing sensitive use the I2S stream isn't the best because you will have some delays between any action and it appearing on the pin (If you look in the issues you might find the calculations for this). For quite a few things it doesn't matter likes the mosfets, but for communication or as a reaction to async events it's not great.

petervanderwalt, 2021-11-12:
Thank you for getting back to me! (:

> Did you configure Marlin properly to have the first 16 bits as the stepper stream and the other 16 bits as the "pins"? If you have the default configuration IIRC all 32bits will be the steppers stream which won't allow you to use them as GPIOs.

Aha!  Did not know about that - I've not found much documentation for the I2S stuff in Marlin, can you point me to details on this?

> Out of the box no, but making the I2S code work over 64 bits instead of 32 should be fairly straightforward.
>
> >
Ahh that explains my other issues then (:  Do you think you can point me or help me achieve that?

And do you have a Paypal donation link by any chance?

simon-jouet, 2021-11-15:
> Aha! Did not know about that - I've not found much documentation for the I2S stuff in Marlin, can you point me to details on this?

You need to have I2S_STEPPER_SPLIT_STREAM defined and it will split the channels into dynamic (the stepper data) and constant (the GPIOs). https://github.com/MarlinFirmware/Marlin/blob/2.0.x/Marlin/src/HAL/ESP32/i2s.cpp#L335

>  I've not found much documentation for the I2S stuff in Marlin

Yeah I've never really written documentations unfortunately, it might be something that happens in the future.

> Ahh that explains my other issues then (: Do you think you can point me or help me achieve that?

I haven't tested yet (I can have a go if needed), but if your look at the ESP32 TRM you will see (page 311) that if Tx FIFO mode0 is set to 2 then it switches to a 32-bit dual channel data. At the moment it's a 16-bit dual channel data (32 bits), so changing to to mode 2 should switch to 64 bits.

So is looks like changing https://github.com/MarlinFirmware/Marlin/blob/2.0.x/Marlin/src/HAL/ESP32/i2s.cpp#L266 from 0 to 2 will allow you to have 64 bits. If you enable the Stepper_split_Stream like above, then you will have 32 bits of stepper stream and 32 for GPIOs.

You could potentially decouple that and use all 64 bits for either but the latency is going to be higher (because in contant mode the next i2s clock will get that data, in stereo mode used for the stepper you will have the latency of the DMA buffers which will be significantly longer)

Closed 2023-06-21.

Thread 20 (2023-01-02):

How to map pins in shift registers?

AlanBig, 2023-01-02:
Hi, friend! Searching the web I came across your extraordinary project with a simple ESP32, I can't understand how you manage to map the number of pins by activating "#define I2S_STEPPER_STREAM" and using shift registers (74hc595 for example), would you be so kind to teach me? Thanks a lot!

AlanBig, 2023-01-19:
Resolved

Closed 2023-01-19.

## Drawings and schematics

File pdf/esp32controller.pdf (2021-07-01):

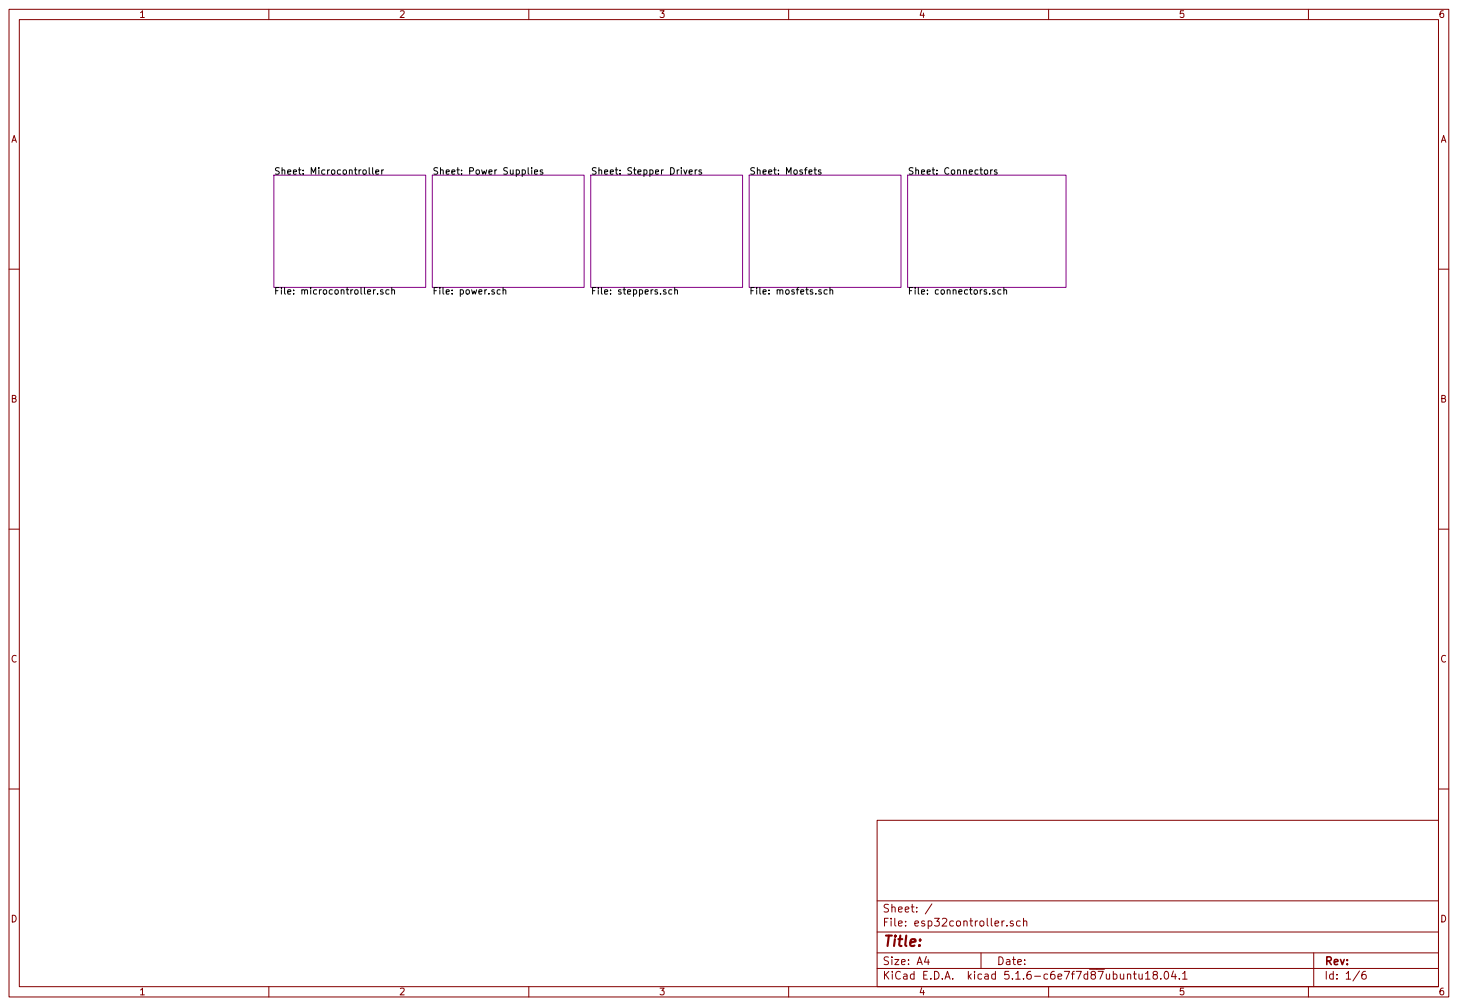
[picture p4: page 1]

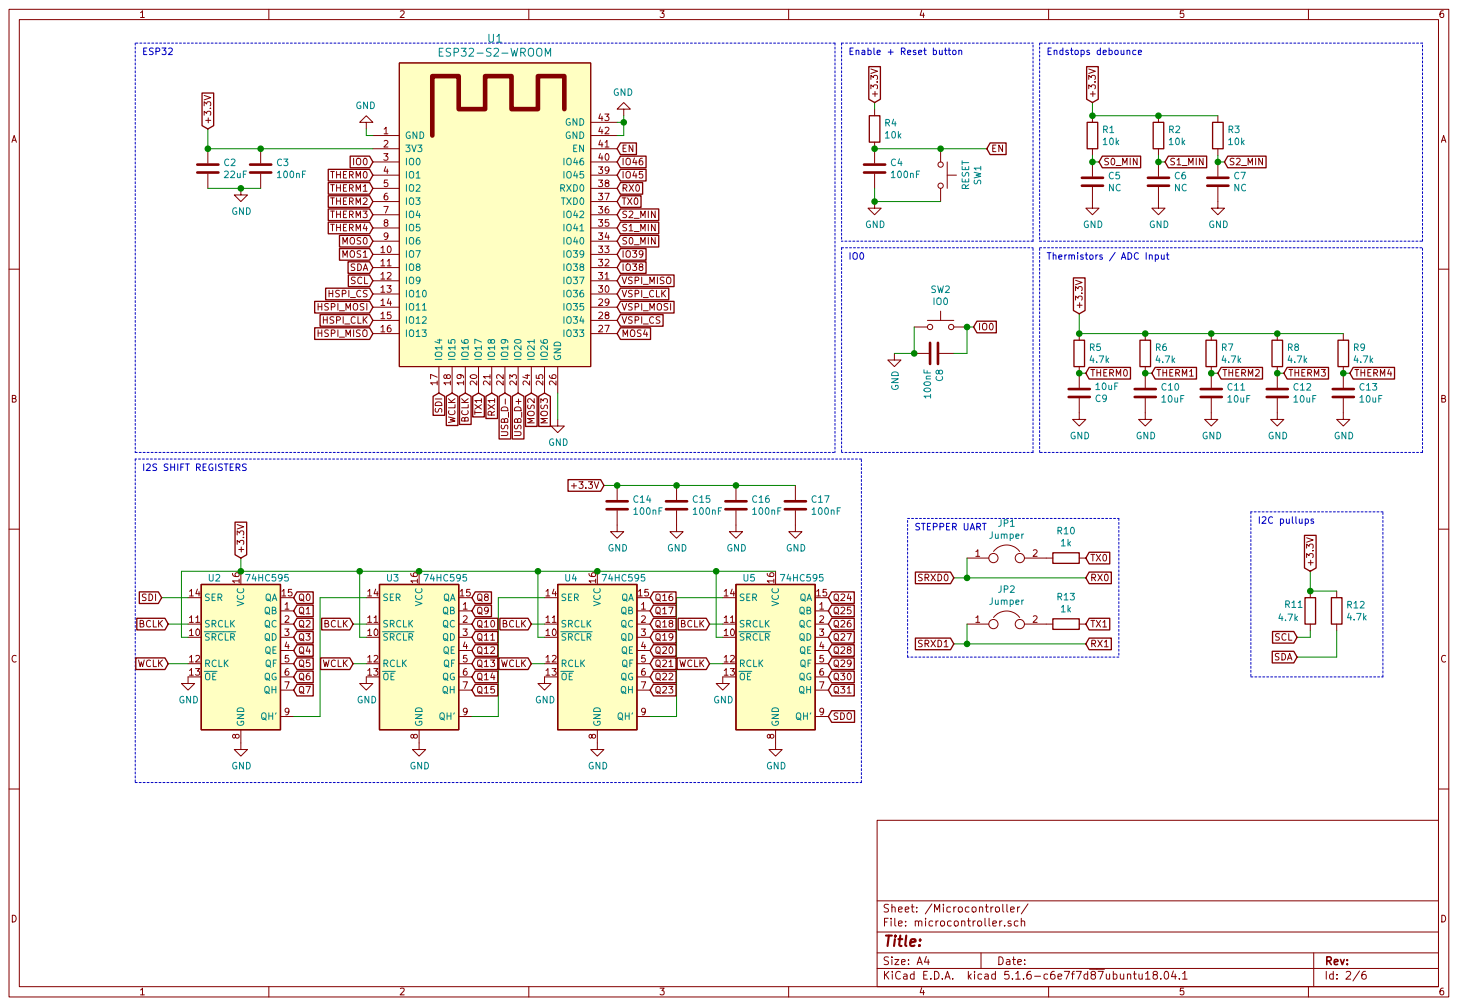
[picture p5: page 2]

8 QH' 9 U3 74HC595 GND GND QB 1 SRCLR 10 SRCLK 11 RCLK 12 OE 13 SER 14 QA 15 VCC 16 QC 2 QD 3 QE 4 QF 5 QG 6 QH 7 GND

8 QH' 9 U5 74HC595 GND GND GND GND QB 1 SRCLR 10 SRCLK 11 RCLK 12 OE 13 SER 14 QA 15 VCC 16 QC 2 QD 3 QE 4 QF 5 QG 6 QH 7 GND

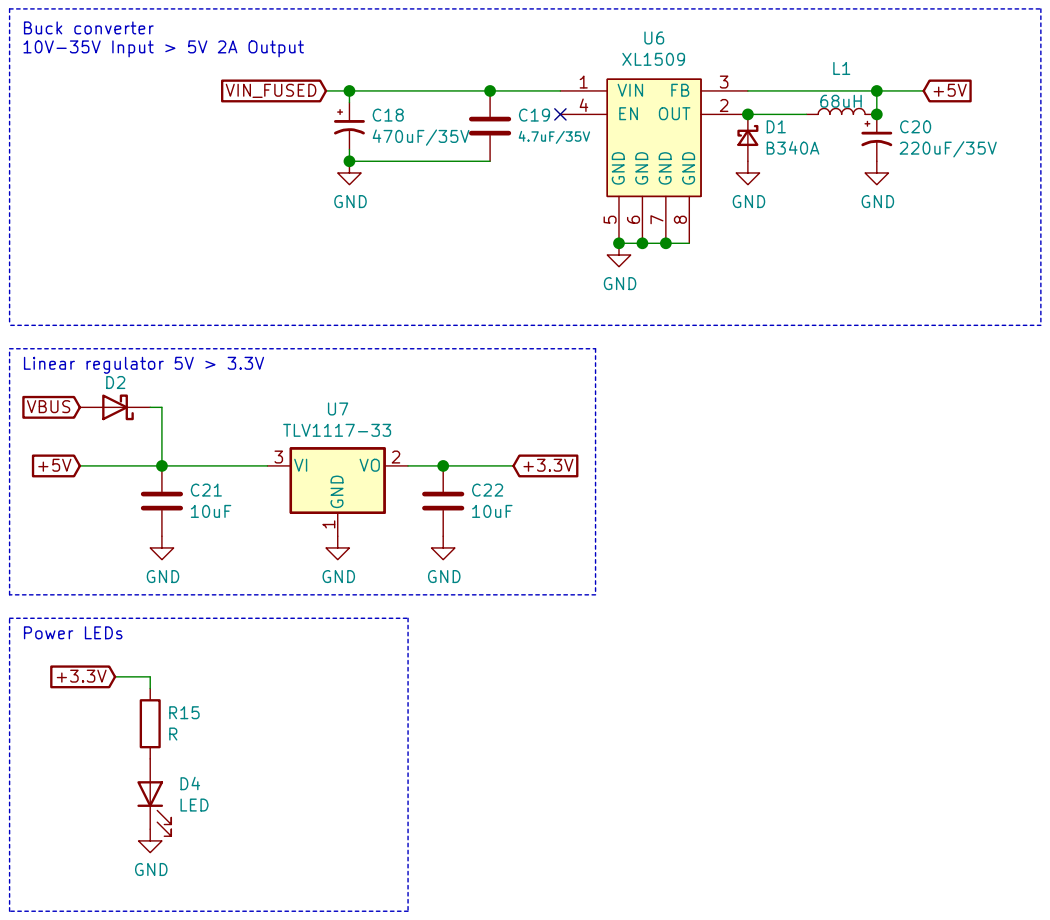
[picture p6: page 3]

Buck converter 10V-35V Input > 5V 2A Output Power LEDs

1 VO 2 VI 3 U7 TLV1117-33 GND GND

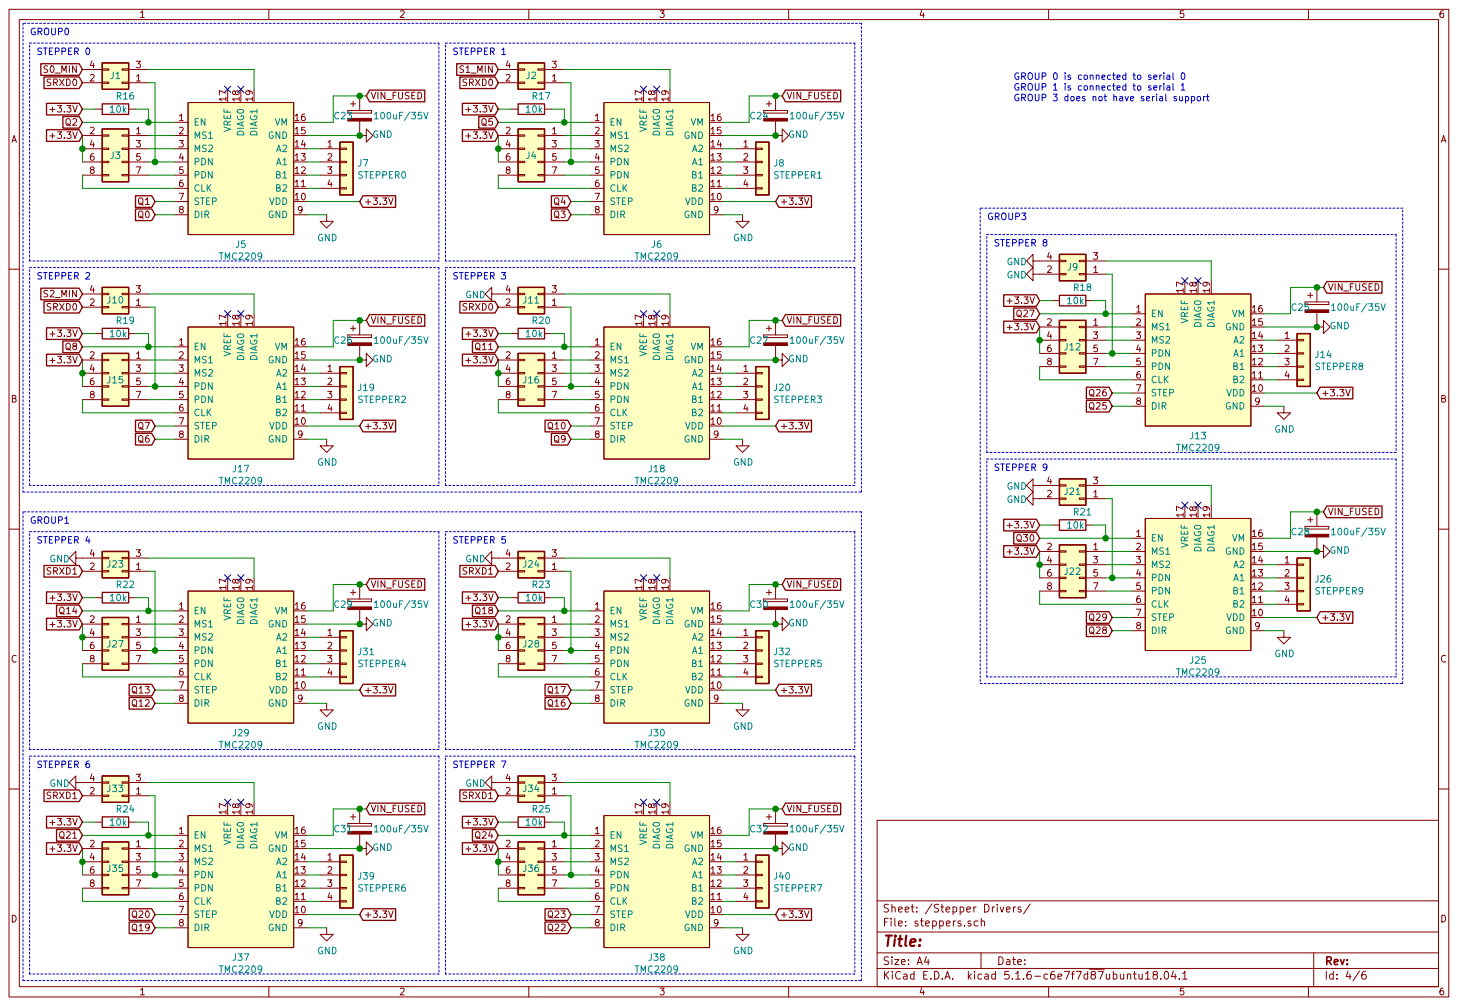
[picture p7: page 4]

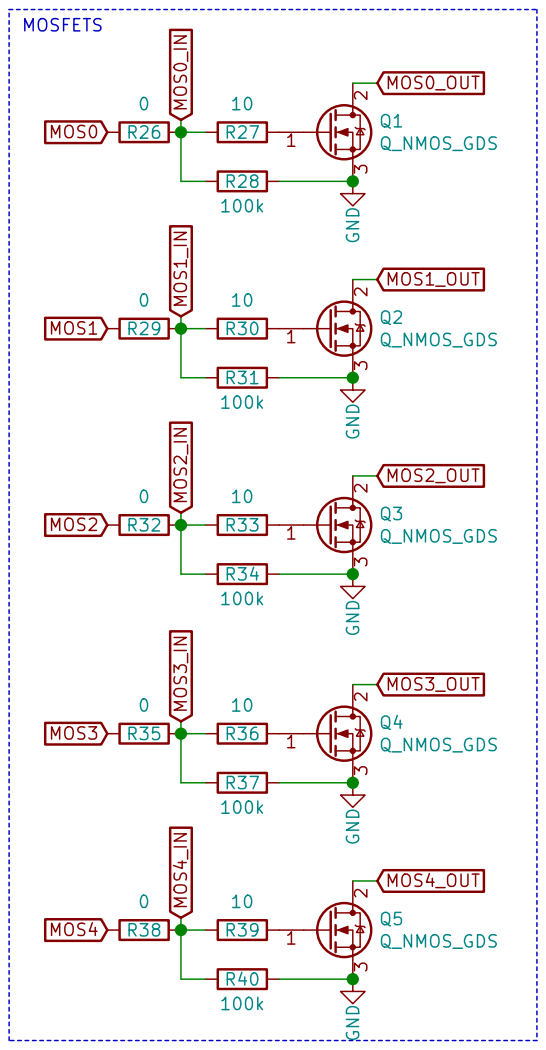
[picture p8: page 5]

Id: 5/6 Title: File: mosfets.sch Sheet: /Mosfets/ R40

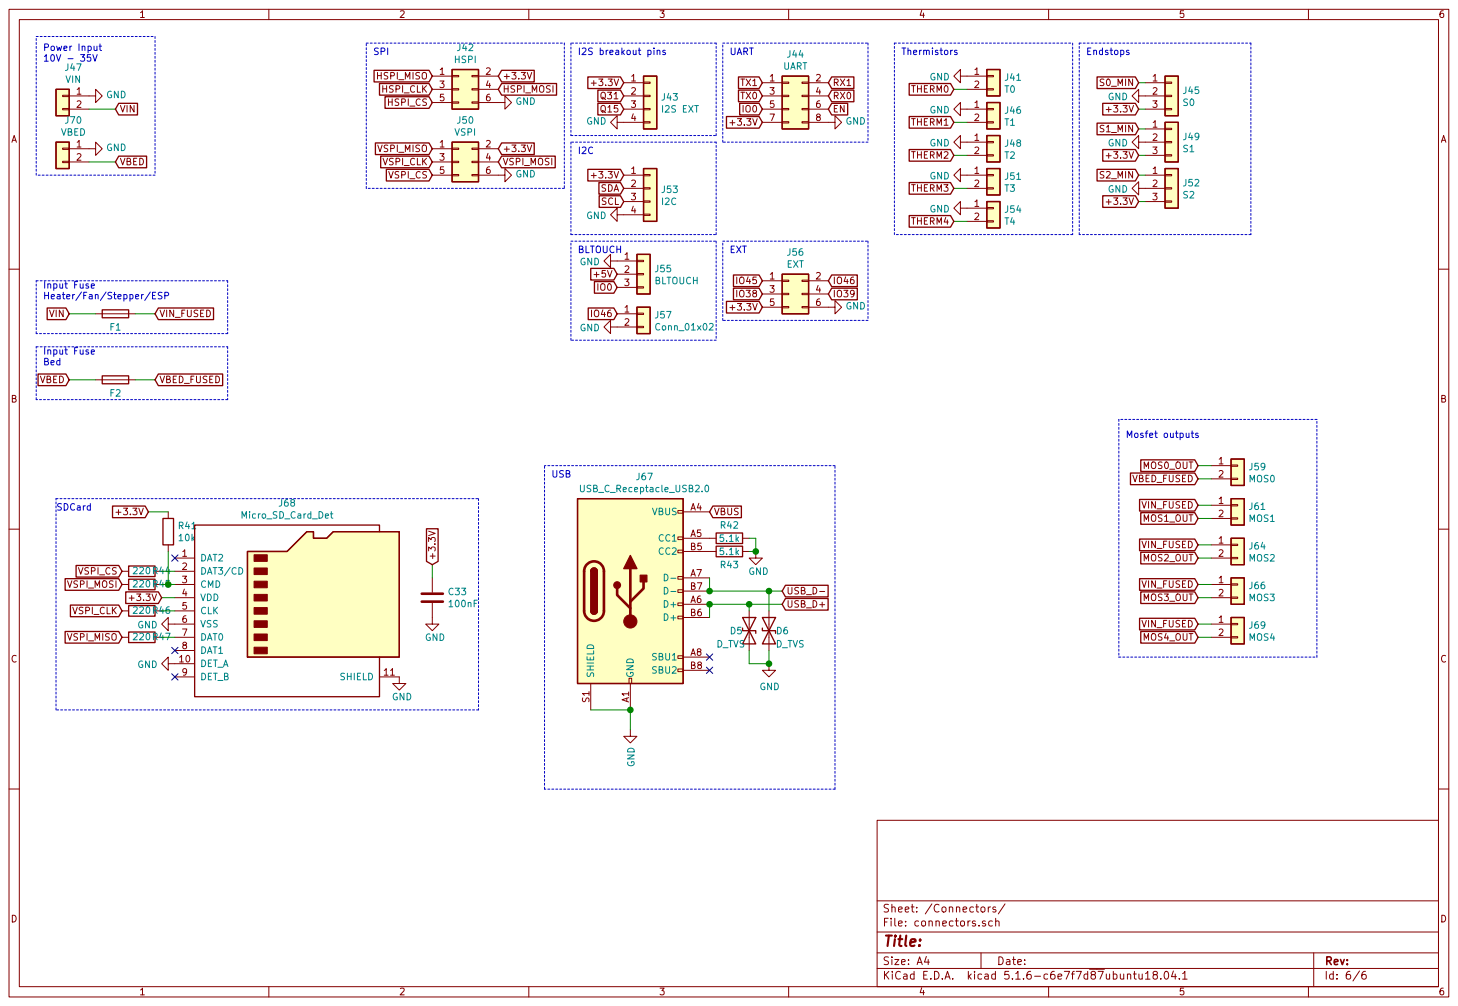
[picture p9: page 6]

Input Fuse
Heater/Fan/Stepper/ESP

Id: 6/6 Title: File: connectors.sch Sheet: /Connectors/

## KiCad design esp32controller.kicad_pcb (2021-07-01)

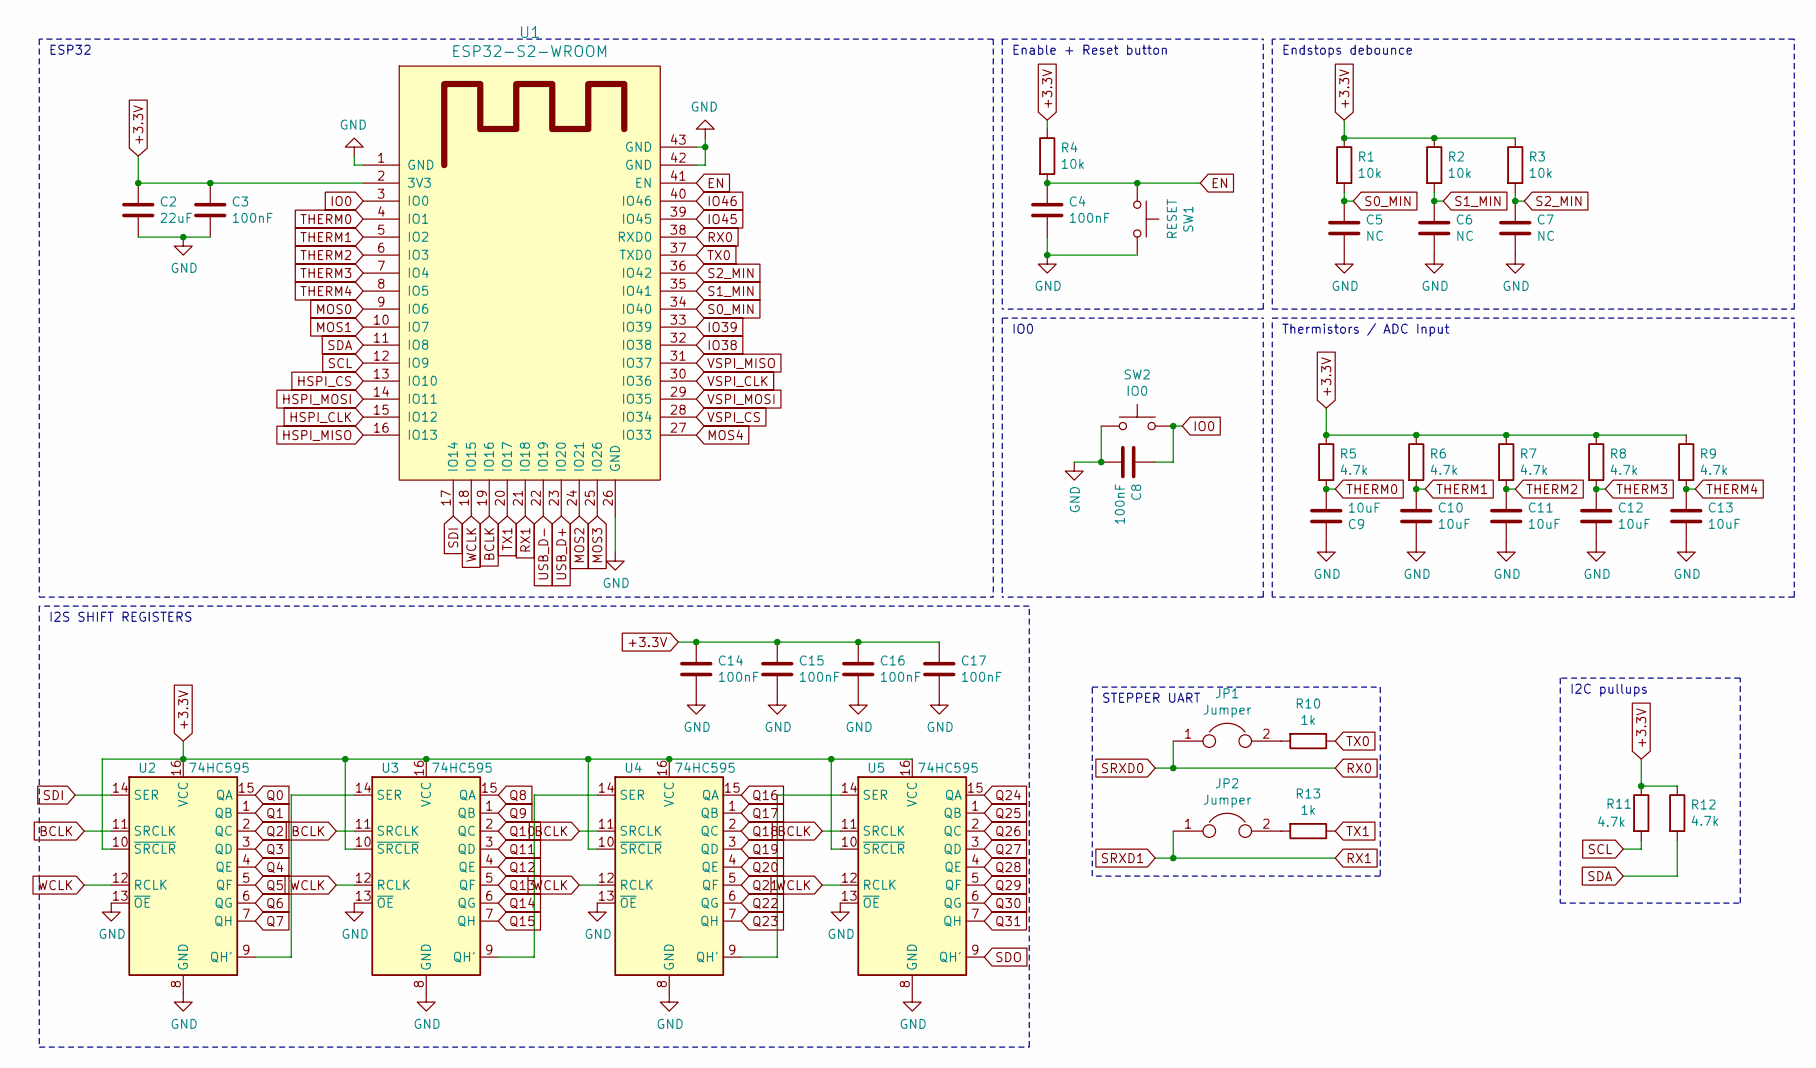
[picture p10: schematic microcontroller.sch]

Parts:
C2: 22uF; C_0805_2012Metric
C3, C4, C8, C14, C15, C16, C17: 100nF; C_0603_1608Metric
C5, C6, C7: NC; C_0603_1608Metric
C9, C10, C11, C12, C13: 10uF; C_0805_2012Metric
JP1, JP2: Jumper; PinHeader_1x02_P2.54mm_Vertical
R1, R2, R3, R4: 10k; R_0603_1608Metric
R5, R6, R7, R8, R9, R11, R12: 4.7k; R_0603_1608Metric
R10, R13: 1k; R_0603_1608Metric
SW1: RESET; SW_Push_1P1T_NO_6x6mm_H9.5mm
SW2: IO0; SW_Push_1P1T_NO_6x6mm_H9.5mm
U1: ESP32-S2-WROOM; esp32-s2-wrooom
U2, U3, U4, U5: 74HC595; TSSOP-16_4.4x5mm_P0.65mm

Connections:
+3.3V: C2.1, C3.1, C14.1, C15.1, C16.1, C17.1, R1.1, R2.1, R3.1, R4.1, R5.1, R6.1, R7.1, R8.1, R9.1, R11.1, R12.1, U1.2 (3V3), U2.10 (~SRCLR), U2.16 (VCC), U3.10 (~SRCLR), U3.16 (VCC), U4.10 (~SRCLR), U4.16 (VCC), U5.10 (~SRCLR), U5.16 (VCC); also elsewhere on the board
BCLK: U1.19 (IO16), U2.11 (SRCLK), U3.11 (SRCLK), U4.11 (SRCLK), U5.11 (SRCLK)
EN: C4.1, R4.2, SW1.1, U1.41 (EN); also elsewhere on the board
GND: C2.2, C3.2, C4.2, C5.2, C6.2, C7.2, C8.2, C9.1, C10.2, C11.2, C12.2, C13.2, C14.2, C15.2, C16.2, C17.2, SW1.2, SW2.1, U1.1 (GND), U1.26 (GND), U1.42 (GND), U1.43 (GND), U2.8 (GND), U2.13 (~OE), U3.8 (GND), U3.13 (~OE), U4.8 (GND), U4.13 (~OE), U5.8 (GND), U5.13 (~OE); also elsewhere on the board
HSPI_CLK: U1.15 (IO12); also elsewhere on the board
HSPI_CS: U1.13 (IO10); also elsewhere on the board
HSPI_MISO: U1.16 (IO13); also elsewhere on the board
HSPI_MOSI: U1.14 (IO11); also elsewhere on the board
IO0: C8.1, SW2.2, U1.3 (IO0); also elsewhere on the board
IO38: U1.32 (IO38); also elsewhere on the board
IO39: U1.33 (IO39); also elsewhere on the board
IO45: U1.39 (IO45); also elsewhere on the board
IO46: U1.40 (IO46); also elsewhere on the board
MOS0: U1.9 (IO6); also elsewhere on the board
MOS1: U1.10 (IO7); also elsewhere on the board
MOS2: U1.24 (IO21); also elsewhere on the board
MOS3: U1.25 (IO26); also elsewhere on the board
MOS4: U1.27 (IO33); also elsewhere on the board
unnamed: JP1.2, R10.2
unnamed: JP2.2, R13.2
unnamed: U2.9 (QH'), U3.14 (SER)
unnamed: U3.9 (QH'), U4.14 (SER)
unnamed: U4.9 (QH'), U5.14 (SER)
Q0: U2.15 (QA); also elsewhere on the board
Q1: U2.1 (QB); also elsewhere on the board
Q2: U2.2 (QC); also elsewhere on the board
Q3: U2.3 (QD); also elsewhere on the board
Q4: U2.4 (QE); also elsewhere on the board
Q5: U2.5 (QF); also elsewhere on the board
Q6: U2.6 (QG); also elsewhere on the board
Q7: U2.7 (QH); also elsewhere on the board
Q8: U3.15 (QA); also elsewhere on the board
Q9: U3.1 (QB); also elsewhere on the board
Q10: U3.2 (QC); also elsewhere on the board
Q11: U3.3 (QD); also elsewhere on the board
Q12: U3.4 (QE); also elsewhere on the board
Q13: U3.5 (QF); also elsewhere on the board
Q14: U3.6 (QG); also elsewhere on the board
Q15: U3.7 (QH); also elsewhere on the board
Q16: U4.15 (QA); also elsewhere on the board
Q17: U4.1 (QB); also elsewhere on the board
Q18: U4.2 (QC); also elsewhere on the board
Q19: U4.3 (QD); also elsewhere on the board
Q20: U4.4 (QE); also elsewhere on the board
Q21: U4.5 (QF); also elsewhere on the board
Q22: U4.6 (QG); also elsewhere on the board
Q23: U4.7 (QH); also elsewhere on the board
Q24: U5.15 (QA); also elsewhere on the board
Q25: U5.1 (QB); also elsewhere on the board
Q26: U5.2 (QC); also elsewhere on the board
Q27: U5.3 (QD); also elsewhere on the board
Q28: U5.4 (QE); also elsewhere on the board
Q29: U5.5 (QF); also elsewhere on the board
Q30: U5.6 (QG); also elsewhere on the board
Q31: U5.7 (QH); also elsewhere on the board
RX0: JP1.1, U1.38 (RXD0); also elsewhere on the board
RX1: JP2.1, U1.21 (IO18); also elsewhere on the board
S0_MIN: C5.1, R1.2, U1.34 (IO40); also elsewhere on the board
S1_MIN: C6.1, R2.2, U1.35 (IO41); also elsewhere on the board
S2_MIN: C7.1, R3.2, U1.36 (IO42); also elsewhere on the board
SCL: R11.2, U1.12 (IO9); also elsewhere on the board
SDA: R12.2, U1.11 (IO8); also elsewhere on the board
SDI: U1.17 (IO14), U2.14 (SER)
THERM0: C9.2, R5.2, U1.4 (IO1); also elsewhere on the board
THERM1: C10.1, R6.2, U1.5 (IO2); also elsewhere on the board
THERM2: C11.1, R7.2, U1.6 (IO3); also elsewhere on the board
THERM3: C12.1, R8.2, U1.7 (IO4); also elsewhere on the board
THERM4: C13.1, R9.2, U1.8 (IO5); also elsewhere on the board
TX0: R10.1, U1.37 (TXD0); also elsewhere on the board
TX1: R13.1, U1.20 (IO17); also elsewhere on the board
USB_D+: U1.23 (IO20); also elsewhere on the board
USB_D-: U1.22 (IO19); also elsewhere on the board
VSPI_CLK: U1.30 (IO36); also elsewhere on the board
VSPI_CS: U1.28 (IO34); also elsewhere on the board
VSPI_MISO: U1.31 (IO37); also elsewhere on the board
VSPI_MOSI: U1.29 (IO35); also elsewhere on the board
WCLK: U1.18 (IO15), U2.12 (RCLK), U3.12 (RCLK), U4.12 (RCLK), U5.12 (RCLK)

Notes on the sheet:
ESP32
I2S SHIFT REGISTERS
Endstops debounce
Enable + Reset button
Thermistors / ADC Input
I2C pullups
IO0
STEPPER UART

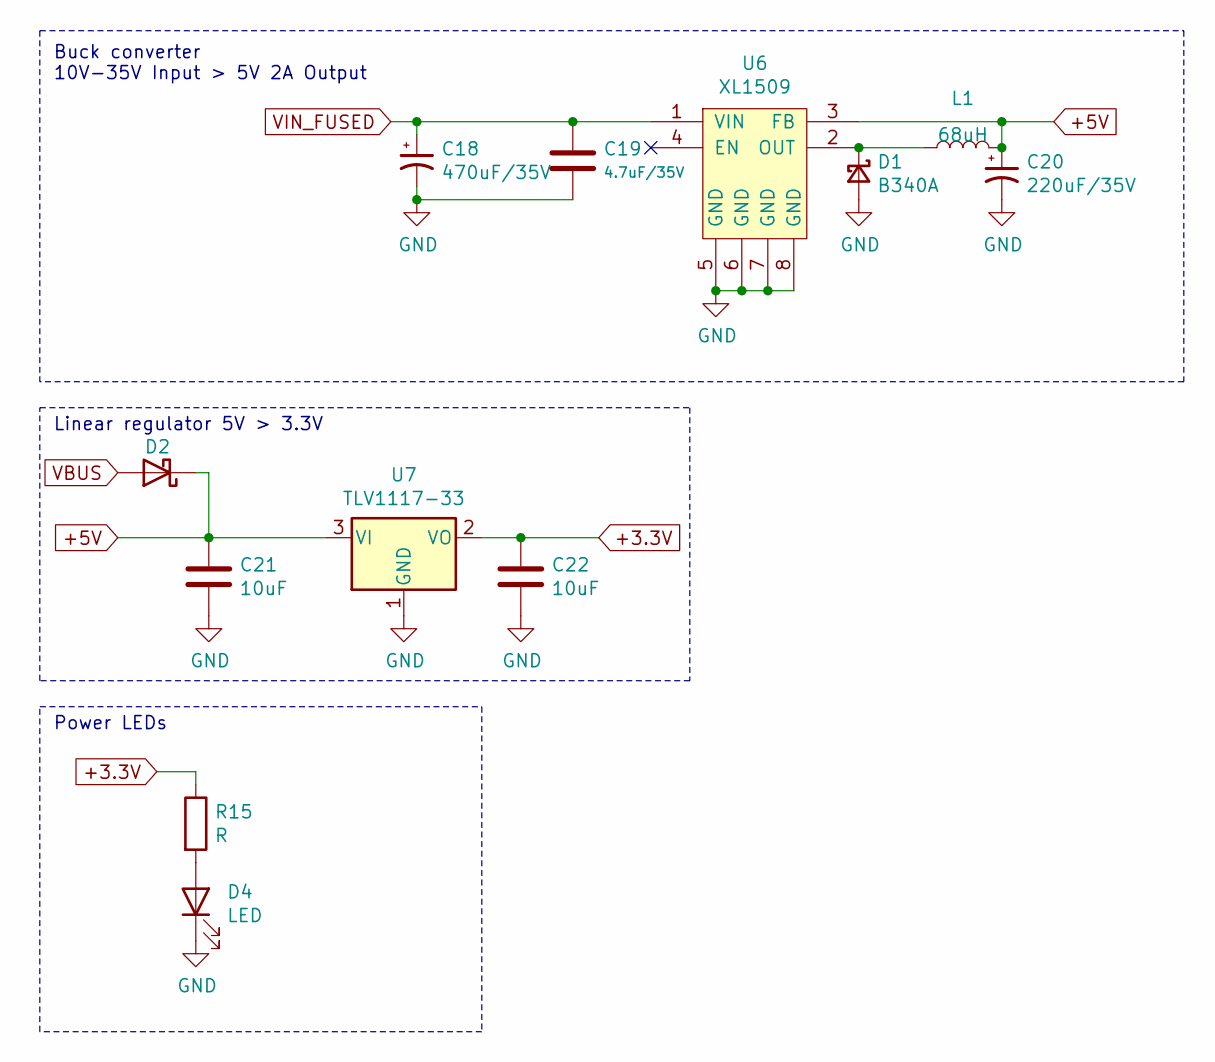
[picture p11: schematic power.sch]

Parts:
C18: 470uF/35V; CP_Elec_10x10
C19: 4.7uF/35V; C_0805_2012Metric
C20: 220uF/35V; C_1210_3225Metric
C21, C22: 10uF; C_0805_2012Metric
D1: B340A; D_SMA
D2: D_Schottky; D_SOD-323_HandSoldering
D4: LED; LED_0805_2012Metric
L1: 68uH; L_7.3x7.3_H3.5
R15: R; R_0603_1608Metric
U6: XL1509; SOIC-8_3.9x4.9mm_P1.27mm
U7: TLV1117-33; SOT-223-3_TabPin2

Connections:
+3.3V: C22.1, R15.1, U7.2 (VO); also elsewhere on the board
+5V: C20.1, C21.1, D2.1 (K), L1.2, U6.3 (FB), U7.3 (VI); also elsewhere on the board
GND: C18.2, C19.2, C20.2, C21.2, C22.2, D1.2 (A), D4.1 (K), U6.5 (GND), U6.6 (GND), U6.7 (GND), U6.8 (GND), U7.1 (GND); also elsewhere on the board
unnamed: D1.1 (K), L1.1, U6.2 (OUT)
unnamed: D4.2 (A), R15.2
VBUS: D2.2 (A); also elsewhere on the board
VIN_FUSED: C18.1, C19.1, U6.1 (VIN); also elsewhere on the board

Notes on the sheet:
Linear regulator 5V > 3.3V
Power LEDs
Buck converter 10V-35V Input > 5V 2A Output

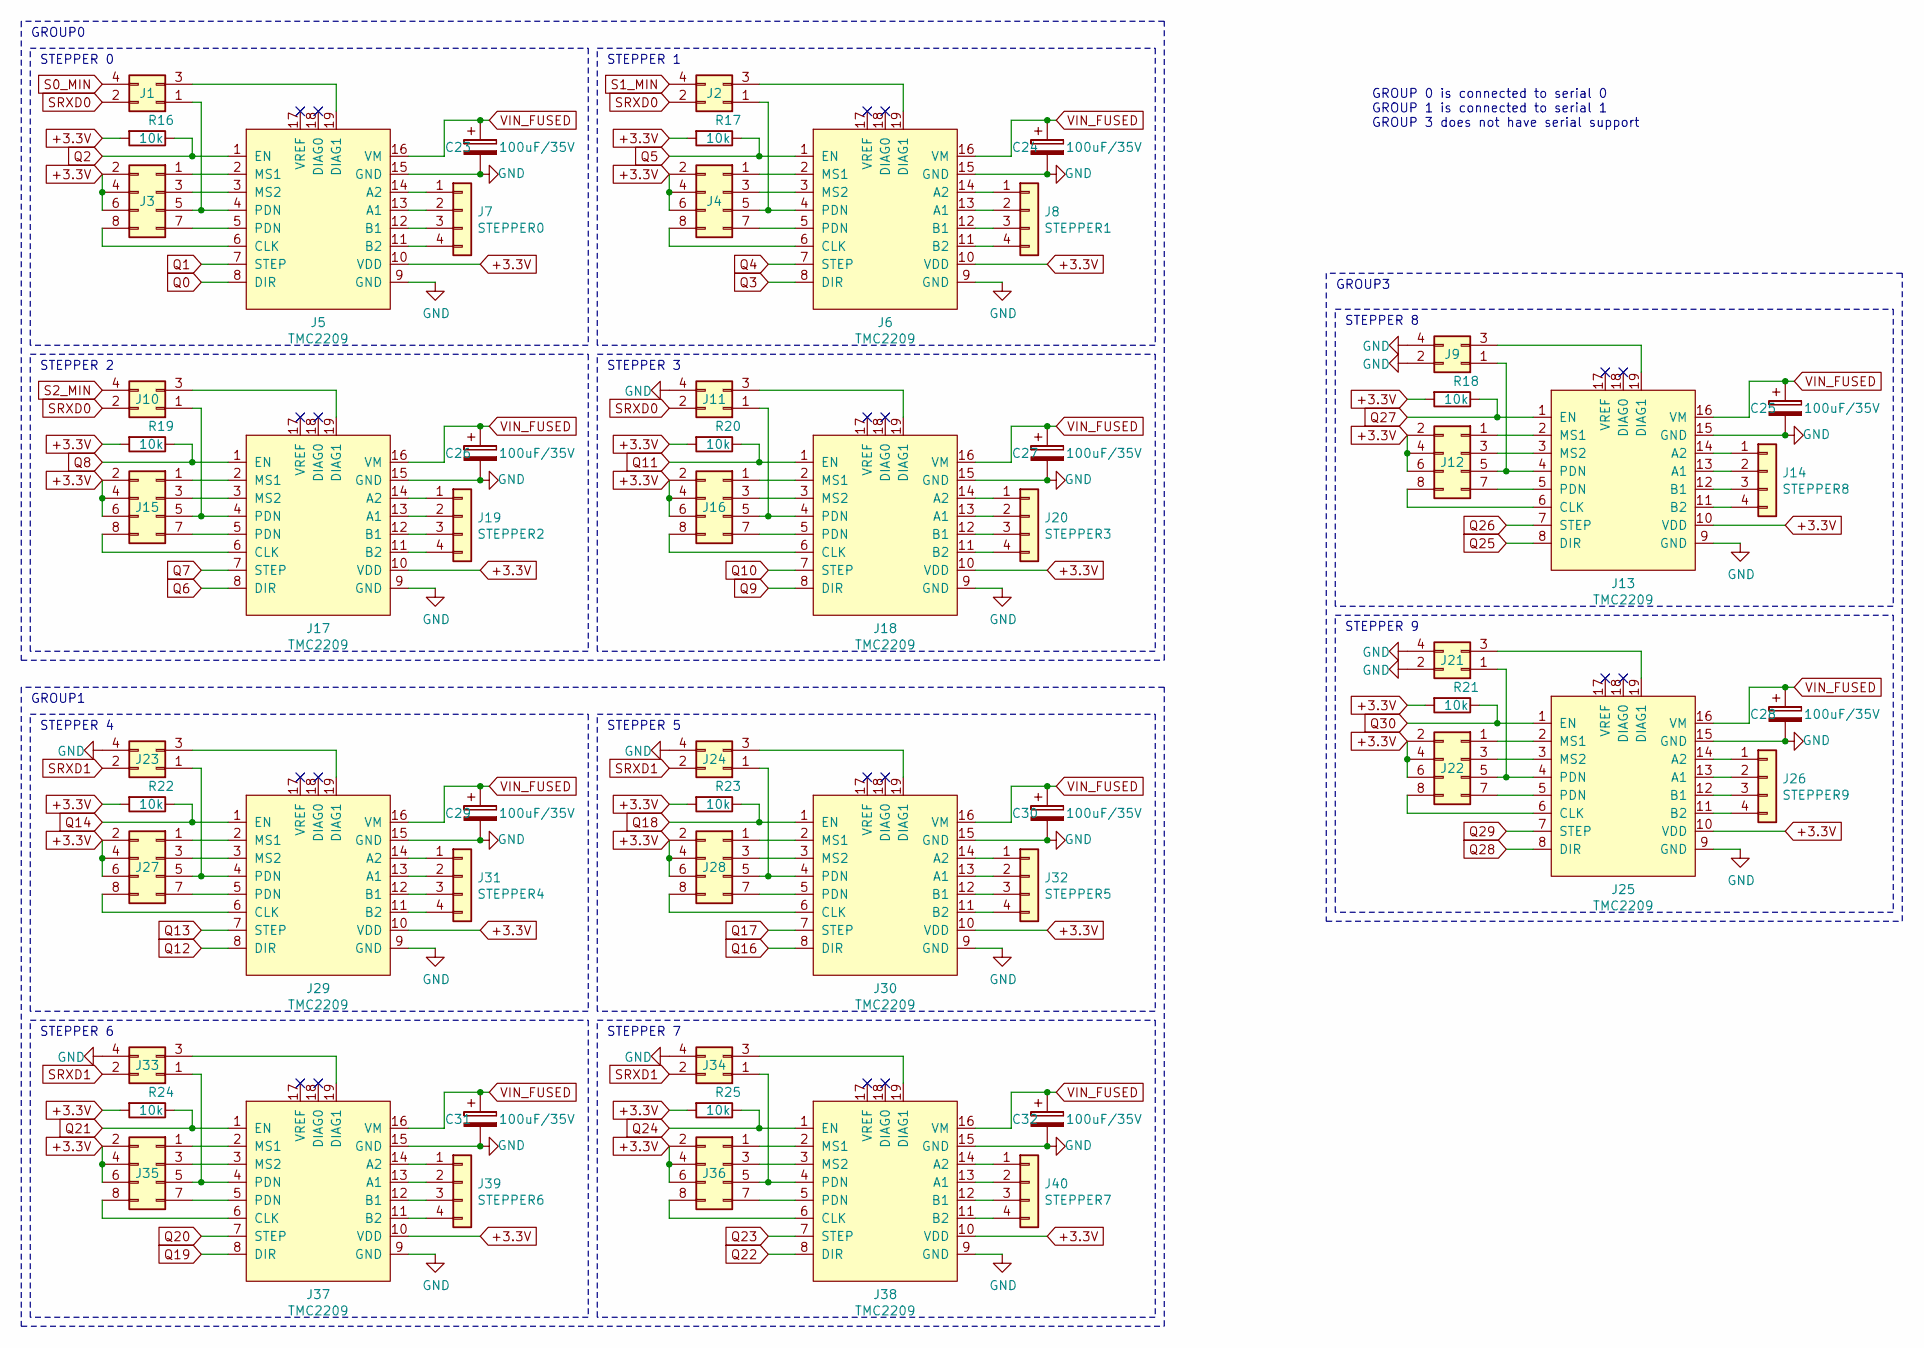
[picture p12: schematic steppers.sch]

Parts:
C23, C24, C25, C26, C27, C28, C29, C30, C31, C32: 100uF/35V; CP_Elec_6.3x7.7
J1, J2, J9, J10, J11, J21, J23, J24, J33, J34: Conn_02x02_Odd_Even; PinHeader_1x04_P2.54mm_Vertical
J3, J4, J12, J15, J16, J22, J27, J28, J35, J36: Conn_02x04_Odd_Even; PinHeader_2x04_P2.54mm_Vertical
J5, J6, J13, J17, J18, J25, J29, J30, J37, J38: TMC2209; pololu
J7: STEPPER0; JST_XH_B4B-XH-A_1x04_P2.50mm_Vertical
J8: STEPPER1; JST_XH_B4B-XH-A_1x04_P2.50mm_Vertical
J14: STEPPER8; JST_XH_B4B-XH-A_1x04_P2.50mm_Vertical
J19: STEPPER2; JST_XH_B4B-XH-A_1x04_P2.50mm_Vertical
J20: STEPPER3; JST_XH_B4B-XH-A_1x04_P2.50mm_Vertical
J26: STEPPER9; JST_XH_B4B-XH-A_1x04_P2.50mm_Vertical
J31: STEPPER4; JST_XH_B4B-XH-A_1x04_P2.50mm_Vertical
J32: STEPPER5; JST_XH_B4B-XH-A_1x04_P2.50mm_Vertical
J39: STEPPER6; JST_XH_B4B-XH-A_1x04_P2.50mm_Vertical
J40: STEPPER7; JST_XH_B4B-XH-A_1x04_P2.50mm_Vertical
R16, R17, R18, R19, R20, R21, R22, R23, R24, R25: 10k; R_0603_1608Metric

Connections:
+3.3V: J3.2, J3.4, J3.6, J4.2, J4.4, J4.6, J5.10 (VDD), J6.10 (VDD), J12.2, J12.4, J12.6, J13.10 (VDD), J15.2, J15.4, J15.6, J16.2, J16.4, J16.6, J17.10 (VDD), J18.10 (VDD), J22.2, J22.4, J22.6, J25.10 (VDD), J27.2, J27.4, J27.6, J28.2, J28.4, J28.6, J29.10 (VDD), J30.10 (VDD), J35.2, J35.4, J35.6, J36.2, J36.4, J36.6, J37.10 (VDD), J38.10 (VDD), R16.2, R17.2, R18.2, R19.2, R20.2, R21.2, R22.2, R23.2, R24.2, R25.2; also elsewhere on the board
GND: C23.2, C24.2, C25.2, C26.2, C27.2, C28.2, C29.2, C30.2, C31.2, C32.2, J5.9 (GND), J5.15 (GND), J6.9 (GND), J6.15 (GND), J9.2, J9.4, J11.4, J13.9 (GND), J13.15 (GND), J17.9 (GND), J17.15 (GND), J18.9 (GND), J18.15 (GND), J21.2, J21.4, J23.4, J24.4, J25.9 (GND), J25.15 (GND), J29.9 (GND), J29.15 (GND), J30.9 (GND), J30.15 (GND), J33.4, J34.4, J37.9 (GND), J37.15 (GND), J38.9 (GND), J38.15 (GND); also elsewhere on the board
unnamed: J1.1, J3.5, J5.4 (PDN)
unnamed: J1.3, J5.19 (DIAG1)
unnamed: J2.1, J4.5, J6.4 (PDN)
unnamed: J2.3, J6.19 (DIAG1)
unnamed: J3.1, J5.2 (MS1)
unnamed: J3.3, J5.3 (MS2)
unnamed: J3.7, J5.5 (PDN)
unnamed: J3.8, J5.6 (CLK)
unnamed: J4.1, J6.2 (MS1)
unnamed: J4.3, J6.3 (MS2)
unnamed: J4.7, J6.5 (PDN)
unnamed: J4.8, J6.6 (CLK)
unnamed: J5.11 (B2), J7.4
unnamed: J5.12 (B1), J7.3
unnamed: J5.13 (A1), J7.2
unnamed: J5.14 (A2), J7.1
unnamed: J6.11 (B2), J8.4
unnamed: J6.12 (B1), J8.3
unnamed: J6.13 (A1), J8.2
unnamed: J6.14 (A2), J8.1
unnamed: J10.1, J15.5, J17.4 (PDN)
unnamed: J10.3, J17.19 (DIAG1)
unnamed: J11.1, J16.5, J18.4 (PDN)
unnamed: J11.3, J18.19 (DIAG1)
unnamed: J12.1, J13.2 (MS1)
unnamed: J12.3, J13.3 (MS2)
unnamed: J9.1, J12.5, J13.4 (PDN)
unnamed: J12.7, J13.5 (PDN)
unnamed: J12.8, J13.6 (CLK)
unnamed: J13.11 (B2), J14.4
unnamed: J13.12 (B1), J14.3
unnamed: J13.13 (A1), J14.2
unnamed: J13.14 (A2), J14.1
unnamed: J9.3, J13.19 (DIAG1)
unnamed: J15.1, J17.2 (MS1)
unnamed: J15.3, J17.3 (MS2)
unnamed: J15.7, J17.5 (PDN)
unnamed: J15.8, J17.6 (CLK)
unnamed: J16.1, J18.2 (MS1)
unnamed: J16.3, J18.3 (MS2)
unnamed: J16.7, J18.5 (PDN)
unnamed: J16.8, J18.6 (CLK)
unnamed: J17.11 (B2), J19.4
unnamed: J17.12 (B1), J19.3
unnamed: J17.13 (A1), J19.2
unnamed: J17.14 (A2), J19.1
unnamed: J18.11 (B2), J20.4
unnamed: J18.12 (B1), J20.3
unnamed: J18.13 (A1), J20.2
unnamed: J18.14 (A2), J20.1
unnamed: J21.1, J22.5, J25.4 (PDN)
unnamed: J21.3, J25.19 (DIAG1)
unnamed: J22.1, J25.2 (MS1)
unnamed: J22.3, J25.3 (MS2)
unnamed: J22.7, J25.5 (PDN)
unnamed: J22.8, J25.6 (CLK)
unnamed: J23.1, J27.5, J29.4 (PDN)
unnamed: J23.3, J29.19 (DIAG1)
unnamed: J24.1, J28.5, J30.4 (PDN)
unnamed: J24.3, J30.19 (DIAG1)
unnamed: J25.11 (B2), J26.4
unnamed: J25.12 (B1), J26.3
unnamed: J25.13 (A1), J26.2
unnamed: J25.14 (A2), J26.1
unnamed: J27.1, J29.2 (MS1)
unnamed: J27.3, J29.3 (MS2)
unnamed: J27.7, J29.5 (PDN)
unnamed: J27.8, J29.6 (CLK)
unnamed: J28.1, J30.2 (MS1)
unnamed: J28.3, J30.3 (MS2)
unnamed: J28.7, J30.5 (PDN)
unnamed: J28.8, J30.6 (CLK)
unnamed: J29.11 (B2), J31.4
unnamed: J29.12 (B1), J31.3
unnamed: J29.13 (A1), J31.2
unnamed: J29.14 (A2), J31.1
unnamed: J30.11 (B2), J32.4
unnamed: J30.12 (B1), J32.3
unnamed: J30.13 (A1), J32.2
unnamed: J30.14 (A2), J32.1
unnamed: J33.1, J35.5, J37.4 (PDN)
unnamed: J33.3, J37.19 (DIAG1)
unnamed: J34.1, J36.5, J38.4 (PDN)
unnamed: J34.3, J38.19 (DIAG1)
unnamed: J35.1, J37.2 (MS1)
unnamed: J35.3, J37.3 (MS2)
unnamed: J35.7, J37.5 (PDN)
unnamed: J35.8, J37.6 (CLK)
unnamed: J36.1, J38.2 (MS1)
unnamed: J36.3, J38.3 (MS2)
unnamed: J36.7, J38.5 (PDN)
unnamed: J36.8, J38.6 (CLK)
unnamed: J37.11 (B2), J39.4
unnamed: J37.12 (B1), J39.3
unnamed: J37.13 (A1), J39.2
unnamed: J37.14 (A2), J39.1
unnamed: J38.11 (B2), J40.4
unnamed: J38.12 (B1), J40.3
unnamed: J38.13 (A1), J40.2
unnamed: J38.14 (A2), J40.1
Q0: J5.8 (DIR); also elsewhere on the board
Q1: J5.7 (STEP); also elsewhere on the board
Q2: J5.1 (EN), R16.1; also elsewhere on the board
Q3: J6.8 (DIR); also elsewhere on the board
Q4: J6.7 (STEP); also elsewhere on the board
Q5: J6.1 (EN), R17.1; also elsewhere on the board
Q6: J17.8 (DIR); also elsewhere on the board
Q7: J17.7 (STEP); also elsewhere on the board
Q8: J17.1 (EN), R19.1; also elsewhere on the board
Q9: J18.8 (DIR); also elsewhere on the board
Q10: J18.7 (STEP); also elsewhere on the board
Q11: J18.1 (EN), R20.1; also elsewhere on the board
Q12: J29.8 (DIR); also elsewhere on the board
Q13: J29.7 (STEP); also elsewhere on the board
Q14: J29.1 (EN), R22.1; also elsewhere on the board
Q16: J30.8 (DIR); also elsewhere on the board
Q17: J30.7 (STEP); also elsewhere on the board
Q18: J30.1 (EN), R23.1; also elsewhere on the board
Q19: J37.8 (DIR); also elsewhere on the board
Q20: J37.7 (STEP); also elsewhere on the board
Q21: J37.1 (EN), R24.1; also elsewhere on the board
Q22: J38.8 (DIR); also elsewhere on the board
Q23: J38.7 (STEP); also elsewhere on the board
Q24: J38.1 (EN), R25.1; also elsewhere on the board
Q25: J13.8 (DIR); also elsewhere on the board
Q26: J13.7 (STEP); also elsewhere on the board
Q27: J13.1 (EN), R18.1; also elsewhere on the board
Q28: J25.8 (DIR); also elsewhere on the board
Q29: J25.7 (STEP); also elsewhere on the board
Q30: J25.1 (EN), R21.1; also elsewhere on the board
RX0: J1.2, J2.2, J10.2, J11.2; also elsewhere on the board
RX1: J23.2, J24.2, J33.2, J34.2; also elsewhere on the board
S0_MIN: J1.4; also elsewhere on the board
S1_MIN: J2.4; also elsewhere on the board
S2_MIN: J10.4; also elsewhere on the board
VIN_FUSED: C23.1, C24.1, C25.1, C26.1, C27.1, C28.1, C29.1, C30.1, C31.1, C32.1, J5.16 (VM), J6.16 (VM), J13.16 (VM), J17.16 (VM), J18.16 (VM), J25.16 (VM), J29.16 (VM), J30.16 (VM), J37.16 (VM), J38.16 (VM); also elsewhere on the board

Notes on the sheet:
STEPPER 0
STEPPER 1
STEPPER 8
STEPPER 2
STEPPER 3
STEPPER 9
STEPPER 4
STEPPER 5
STEPPER 6
STEPPER 7
GROUP0
GROUP1
GROUP 0 is connected to serial 0 GROUP 1 is connected to serial 1 GROUP 3 does not have serial support
GROUP3

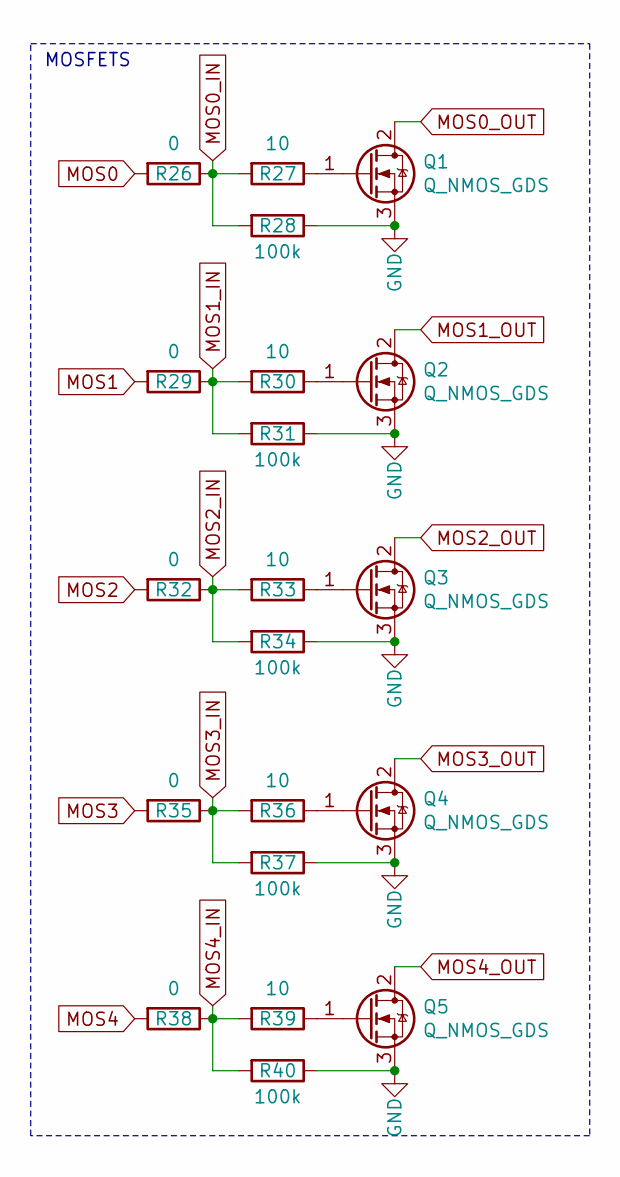
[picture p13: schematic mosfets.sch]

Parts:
Q1, Q2, Q3, Q4, Q5: Q_NMOS_GDS; TO-252-2
R26, R29, R32, R35, R38: 0; R_0603_1608Metric
R27, R30, R33, R36, R39: 10; R_0603_1608Metric
R28, R31, R34, R37, R40: 100k; R_0603_1608Metric

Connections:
GND: Q1.3 (S), Q2.3 (S), Q3.3 (S), Q4.3 (S), Q5.3 (S), R28.1, R31.1, R34.1, R37.1, R40.1; also elsewhere on the board
MOS0: R26.2; also elsewhere on the board
MOS0_IN: R26.1, R27.2, R28.2
MOS0_OUT: Q1.2 (D); also elsewhere on the board
MOS1: R29.2; also elsewhere on the board
MOS1_IN: R29.1, R30.2, R31.2
MOS1_OUT: Q2.2 (D); also elsewhere on the board
MOS2: R32.2; also elsewhere on the board
MOS2_IN: R32.1, R33.2, R34.2
MOS2_OUT: Q3.2 (D); also elsewhere on the board
MOS3: R35.2; also elsewhere on the board
MOS3_IN: R35.1, R36.2, R37.2
MOS3_OUT: Q4.2 (D); also elsewhere on the board
MOS4: R38.2; also elsewhere on the board
MOS4_IN: R38.1, R39.2, R40.2
MOS4_OUT: Q5.2 (D); also elsewhere on the board
unnamed: Q1.1 (G), R27.1
unnamed: Q2.1 (G), R30.1
unnamed: Q3.1 (G), R33.1
unnamed: Q4.1 (G), R36.1
unnamed: Q5.1 (G), R39.1

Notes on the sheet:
MOSFETS

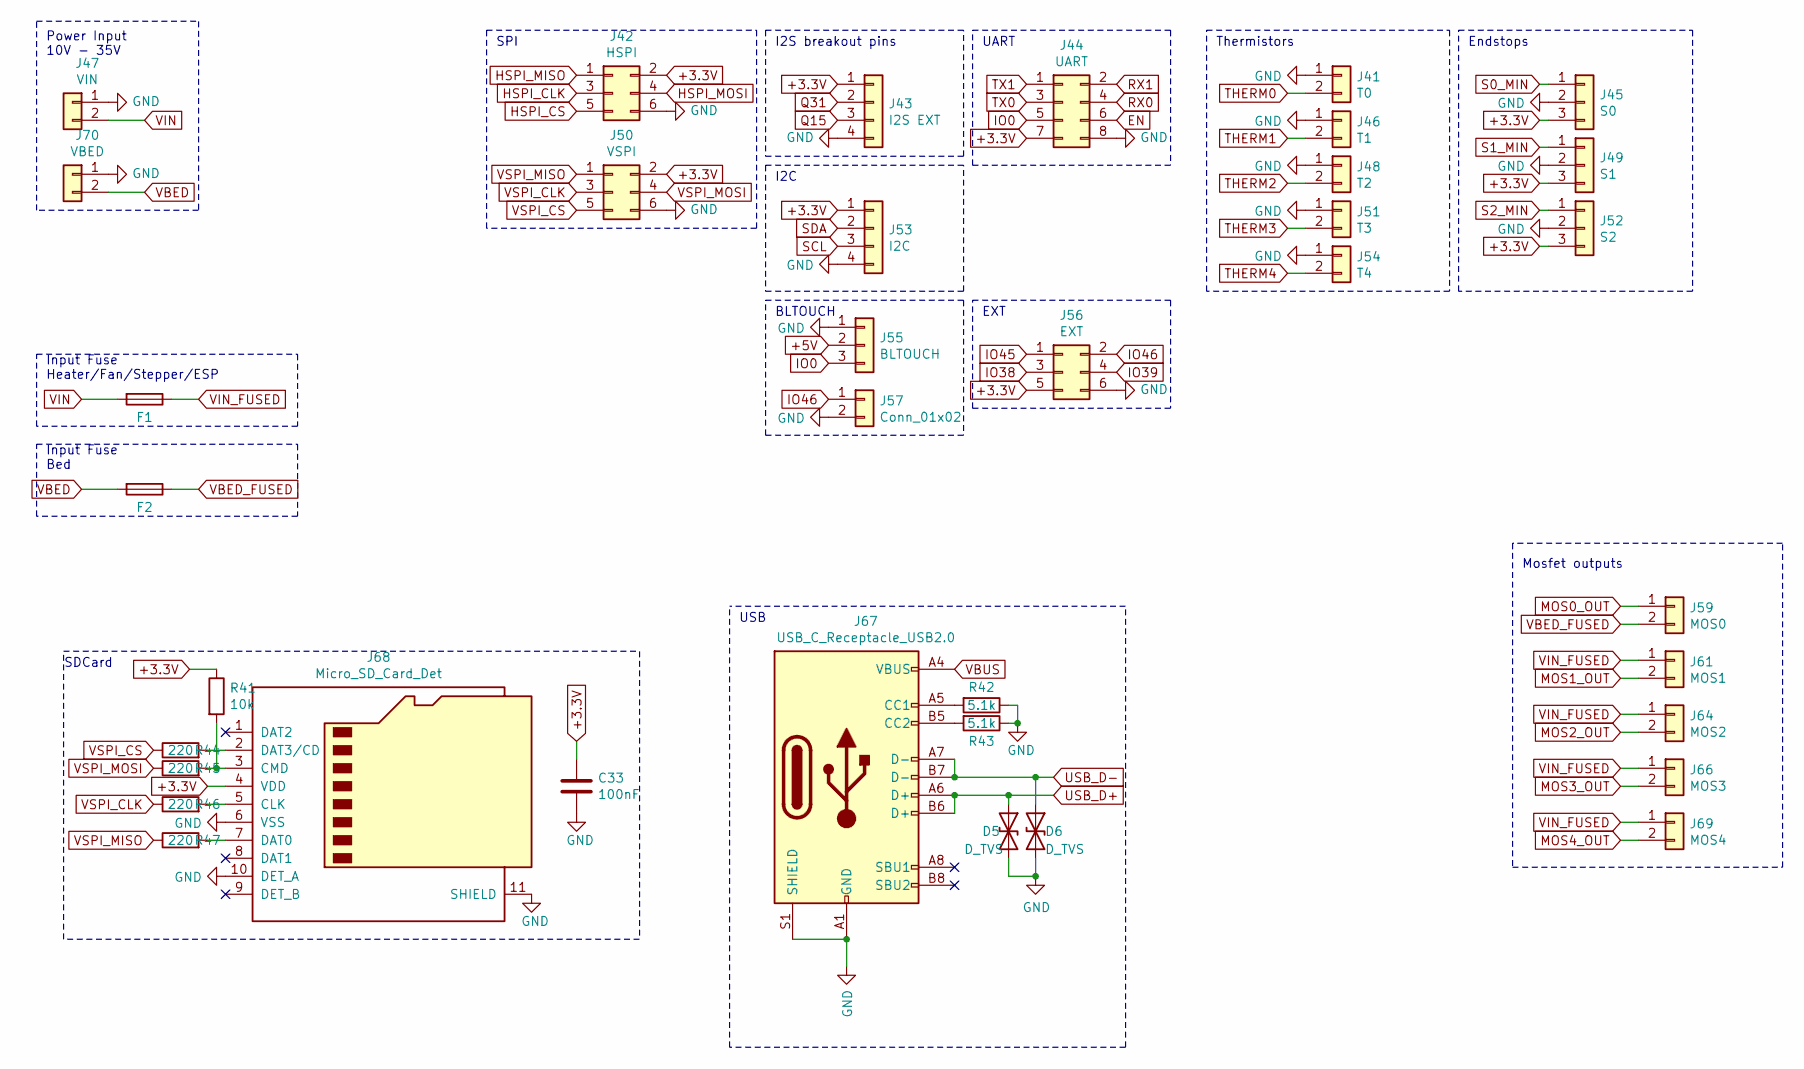
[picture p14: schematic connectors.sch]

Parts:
C33: 100nF; C_0603_1608Metric
D5, D6: D_TVS; D_SOD-523
F1, F2: Fuse; Fuse_holder_0679H
J41: T0; JST_XH_B2B-XH-A_1x02_P2.50mm_Vertical
J42: HSPI; IDC-Header_2x03_P2.54mm_Vertical
J43: I2S EXT; JST_XH_B4B-XH-A_1x04_P2.50mm_Vertical
J44: UART; IDC-Header_2x04_P2.54mm_Vertical
J45: S0; JST_XH_B3B-XH-A_1x03_P2.50mm_Vertical
J46: T1; JST_XH_B2B-XH-A_1x02_P2.50mm_Vertical
J47: VIN; TERM_2-WAY_6.35mm
J48: T2; JST_XH_B2B-XH-A_1x02_P2.50mm_Vertical
J49: S1; JST_XH_B3B-XH-A_1x03_P2.50mm_Vertical
J50: VSPI; IDC-Header_2x03_P2.54mm_Vertical
J51: T3; JST_XH_B2B-XH-A_1x02_P2.50mm_Vertical
J52: S2; JST_XH_B3B-XH-A_1x03_P2.50mm_Vertical
J53: I2C; JST_XH_B4B-XH-A_1x04_P2.50mm_Vertical
J54: T4; JST_XH_B2B-XH-A_1x02_P2.50mm_Vertical
J55: BLTOUCH; PinHeader_1x03_P2.54mm_Vertical
J56: EXT; IDC-Header_2x03_P2.54mm_Vertical
J57: Conn_01x02; PinHeader_1x02_P2.54mm_Vertical
J59: MOS0; TERM_2-WAY_6.35mm
J61: MOS1; TerminalBlock_bornier-2_P5.08mm
J64: MOS2; TerminalBlock_bornier-2_P5.08mm
J66: MOS3; TerminalBlock_bornier-2_P5.08mm
J67: USB_C_Receptacle_USB2.0; USB_C
J68: Micro_SD_Card_Det; microsd
J69: MOS4; TerminalBlock_bornier-2_P5.08mm
J70: VBED; TERM_2-WAY_6.35mm
R41: 10k; R_0603_1608Metric
R42, R43: 5.1k; R_0603_1608Metric
R44, R45, R46, R47: 220; R_0603_1608Metric

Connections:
+3.3V: C33.1, J42.2, J43.1, J44.7, J45.3, J49.3, J50.2, J52.3, J53.1, J56.5, J68.4 (VDD), R41.1; also elsewhere on the board
+5V: J55.2; also elsewhere on the board
EN: J44.6; also elsewhere on the board
GND: C33.2, D5.2 (A2), D6.2 (A2), J41.1, J42.6, J43.4, J44.8, J45.2, J46.1, J47.1, J48.1, J49.2, J50.6, J51.1, J52.2, J53.4, J54.1, J55.1, J56.6, J57.2, J67.A1 (GND), J67.A12 (GND), J67.B1 (GND), J67.B12 (GND), J67.S1 (SHIELD), J68.6 (VSS), J68.10 (DET_A), J68.11 (SHIELD), J70.1, R42.1, R43.1; also elsewhere on the board
HSPI_CLK: J42.3; also elsewhere on the board
HSPI_CS: J42.5; also elsewhere on the board
HSPI_MISO: J42.1; also elsewhere on the board
HSPI_MOSI: J42.4; also elsewhere on the board
IO0: J44.5, J55.3; also elsewhere on the board
IO38: J56.3; also elsewhere on the board
IO39: J56.4; also elsewhere on the board
IO45: J56.1; also elsewhere on the board
IO46: J56.2, J57.1; also elsewhere on the board
MOS0_OUT: J59.1; also elsewhere on the board
MOS1_OUT: J61.2; also elsewhere on the board
MOS2_OUT: J64.2; also elsewhere on the board
MOS3_OUT: J66.2; also elsewhere on the board
MOS4_OUT: J69.2; also elsewhere on the board
unnamed: J67.A5 (CC1), R42.2
unnamed: J67.B5 (CC2), R43.2
unnamed: J68.2 (DAT3/CD), R44.2
unnamed: J68.3 (CMD), R41.2, R45.2
unnamed: J68.5 (CLK), R46.2
unnamed: J68.7 (DAT0), R47.2
Q15: J43.3; also elsewhere on the board
Q31: J43.2; also elsewhere on the board
RX0: J44.4; also elsewhere on the board
RX1: J44.2; also elsewhere on the board
S0_MIN: J45.1; also elsewhere on the board
S1_MIN: J49.1; also elsewhere on the board
S2_MIN: J52.1; also elsewhere on the board
SCL: J53.3; also elsewhere on the board
SDA: J53.2; also elsewhere on the board
THERM0: J41.2; also elsewhere on the board
THERM1: J46.2; also elsewhere on the board
THERM2: J48.2; also elsewhere on the board
THERM3: J51.2; also elsewhere on the board
THERM4: J54.2; also elsewhere on the board
TX0: J44.3; also elsewhere on the board
TX1: J44.1; also elsewhere on the board
USB_D+: D5.1 (A1), J67.A6 (D+), J67.B6 (D+); also elsewhere on the board
USB_D-: D6.1 (A1), J67.A7 (D-), J67.B7 (D-); also elsewhere on the board
VBED: F2.2, J70.2
VBED_FUSED: F2.1, J59.2
VBUS: J67.A4 (VBUS), J67.A9 (VBUS), J67.B4 (VBUS), J67.B9 (VBUS); also elsewhere on the board
VIN: F1.2, J47.2
VIN_FUSED: F1.1, J61.1, J64.1, J66.1, J69.1; also elsewhere on the board
VSPI_CLK: J50.3, R46.1; also elsewhere on the board
VSPI_CS: J50.5, R44.1; also elsewhere on the board
VSPI_MISO: J50.1, R47.1; also elsewhere on the board
VSPI_MOSI: J50.4, R45.1; also elsewhere on the board

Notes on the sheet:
Endstops
Power Input 10V - 35V
Input Fuse Heater/Fan/Stepper/ESP
Input Fuse Bed
I2S breakout pins
Mosfet outputs
Thermistors
SDCard
USB
SPI
I2C
UART
BLTOUCH
EXT

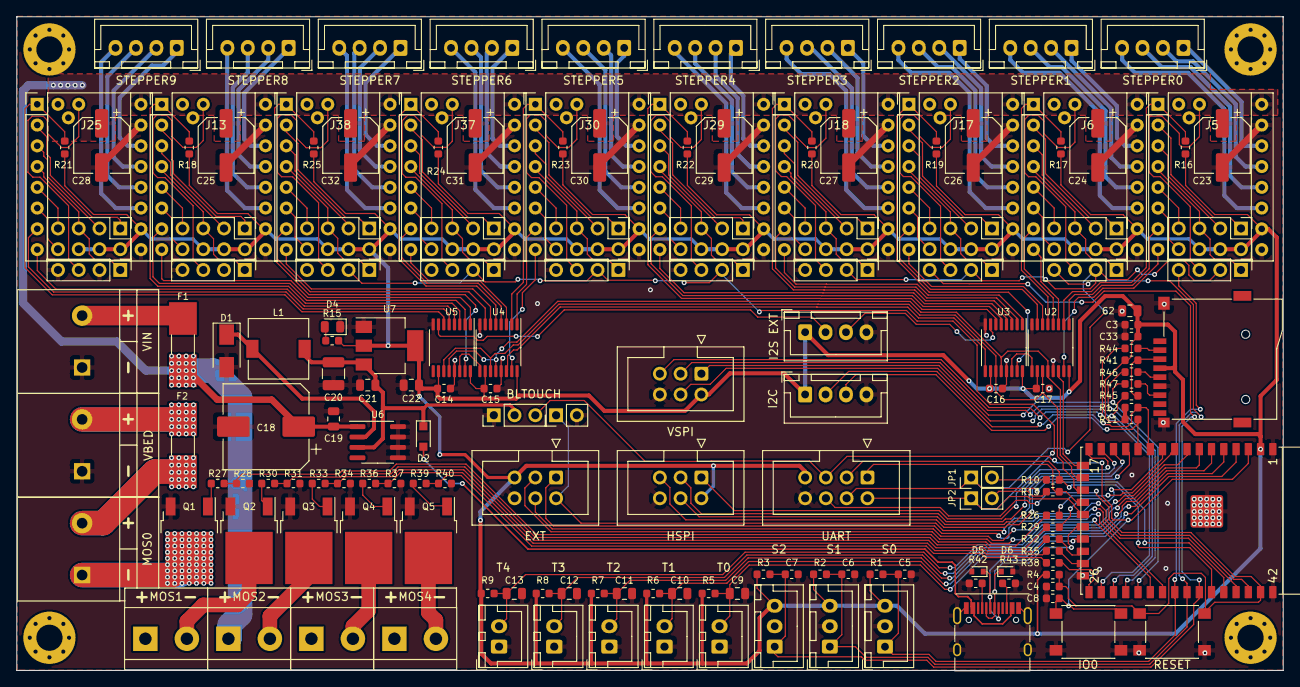
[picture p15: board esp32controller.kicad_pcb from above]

Board: 2 copper layers, 155.0 x 80.0 mm, 167 parts (0 on the bottom side), 206 nets.

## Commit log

2018-07-05 Prototype R1
    [esp32controller.kicad_pcb, esp32controller.sch]
2021-07-01 Prototype R2
    [comms.sch, connectors.sch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]
2021-07-01 Prototype R3
    [comms.sch, connectors.sch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]
